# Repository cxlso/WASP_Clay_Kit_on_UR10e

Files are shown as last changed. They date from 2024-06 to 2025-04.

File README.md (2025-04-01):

# WASP Clay Kit on UR10e
###### A controller box and mounts to get started with the WASP Clay Kit on UR10e

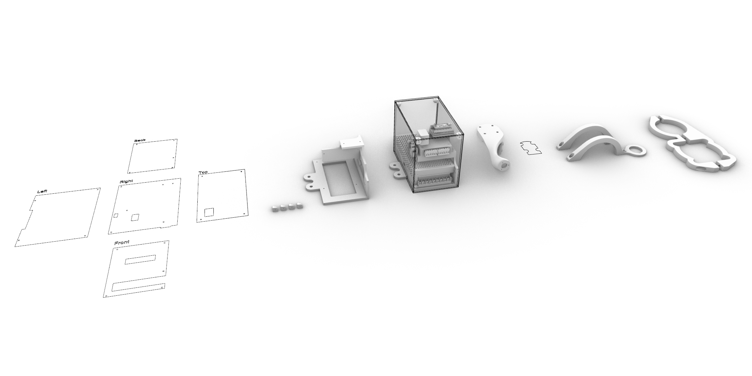
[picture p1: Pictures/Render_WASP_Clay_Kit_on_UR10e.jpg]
Render_MDPH2_on_UR10e


## Overview
This repository contains everything needed to get started with robotic clay printing with the [WASP Clay Kit](https://www.3dwasp.shop/en/prodotto/clay-extruder-wasp-clay-kit/) and the [Universal Robot UR10e](https://www.universal-robots.com/products/ur10-robot/) (or any UR model).

Included in the repository are:

- Controller Box CAD Files: For 3D printing the structure and laser cutting the acrylic walls of the controller box,
- Mounts CAD Files: For 3d printing mounts to secure the clay tank, extruder, and pressure gauge,
- Scripts: Arduino code for the controller and Grasshopper toolpath example.

## Note on the Signal Workflow

The workflow begins with the Grasshopper script embedding the extrusion commands (rate and direction) into the URP file. This file instructs the UR10e to output two analog voltage signals (0-5V) on AO0 (Pul) and AO1 (Dir). These signals are read by the Arduino on pins A0 (Pul) and A1 (Dir), which translates them into digital signals on pins D2 (Pul) and D3 (Dir) for the stepper motor driver, ultimately driving the WASP extruder's stepper motor.

The analog signals can also be overwritten in real-time using the UR Teaching Pendant.

**Grasshopper (Extrusion Command Embeded in URP file/G-Code ) ⟶ UR10e (Analog Output 0-5V) ⟶ Arduino (Analog Input) ⟶ Stepper Motor Driver (Digital Signal) ⟶ WASP Extruder's Stepper Motor**

## Components

- Arduino Nano
- TM6600 Stepper Motor Driver
- LM2596 Stepdown reducer 24v to 12v
- Rocker Switch
- 24v Power Supply
- M3 and M4 Hex Socket Head Screws
- 3mm Acrylic Sheet
- Electrical Connectors (JST XH in our case)
- 18 and 24awg cables 

## Setup and Installation
### Prerequisites

- UR10e Robotic Arm (or any UR models),
- WASP Clay kit (WASP LDM Extruder 3.0, Clay Tank),
- Rhino Grasshopper: For generating toolpath commands.

### Wiring Diagram

Refer to the following wiring diagram for the electrical connections.

LDM_WASP_Extruder_3.0_on_UR10e_Wiring_Diagram
Diagram made with the open-source tool [Fritzing](https://fritzing.org/).

### CAD Files

#### Controller Box

- [Structure](Controller_Box/CAD/Print_WASP_Skeleton.stl) 3D printing file. Skeleton inside de box holding all the components in place,
- [Corner brackets](Controller_Box/CAD/Print_WASP_Corner_Bracket.stl) 3D printing file,
- [3MM acrylic wall](Controller_Box/CAD/Cut_WASP_3MM_Walls.AI) Laser cutting file.

#### Mounts
- [WASP LDM Extruder 3.0 Mount](Mounts/Print_WASP_Extruder_Mount.stl) 3D printing file,
- [Clay Tank Mount](Mounts/Print_WASP_Tank_Mount.stl) 3D printing file,
- [Pressure Gauge Mount](Mounts/Print_WASP_Gauge_Mount.stl) 3D printing file.

If customization is desired, Rhino files for each of the parts are in the repository.

### Scripts

#### [Arduino Script](Arduino/Stepper_PulseDir_WASP)

Upload the provided code to the Arduino Nano. Ensure all connections are made according to the wiring diagram.

#### [Grasshopper Definition](Grasshopper/Basic_Robotic_Extrusion_WASP.gh)

The [Robots](https://www.food4rhino.com/en/app/robots) plugin is necessary. The extrusion rate is set in RPM and is converted to steps per second with the following equation:
$$y = \left( \frac{x \times 800}{60} \right)$$
Where 800 represents the number of steps per revolution for the stepper motor, and 60 is used to convert minutes to seconds, resulting in the conversion of RPM (x) to steps per second (y).

## Pictures and Videos

https://github.com/cxlso/WASP_Clay_Kit_on_UR10e/assets/29285706/da89046f-a3ae-4ad9-899d-0b77da0f6eef

      

## Contributing

Contributions are welcome! Please submit a pull request or open an issue to discuss any changes or improvements.

## License

[][cc-by-nc-sa]

This work is licensed under a
[Creative Commons Attribution-NonCommercial-ShareAlike 4.0 International License][cc-by-nc-sa].

[][cc-by-nc-sa]

[cc-by-nc-sa]: http://creativecommons.org/licenses/by-nc-sa/4.0/
[cc-by-nc-sa-image]: https://licensebuttons.net/l/by-nc-sa/4.0/88x31.png
[cc-by-nc-sa-shield]: https://img.shields.io/badge/License-CC%20BY--NC--SA%204.0-lightgrey.svg

## Acknowledgements

Special thanks to [Luigi Pacheco](https://luigipacheco.com/) and [Bhavleen Kaur](https://bhavleenkaurnarula.wordpress.com/) from the [FIU RDFlab](https://rdflabfiu.github.io/labwiki/) for the tips.

This project was developed on my own initiative at the [School of Architecture of Florida Atlantic University](https://www.fau.edu/artsandletters/architecture/) within the Environmental Design and Natural Materials lab, directed by Shermeen Yousif.

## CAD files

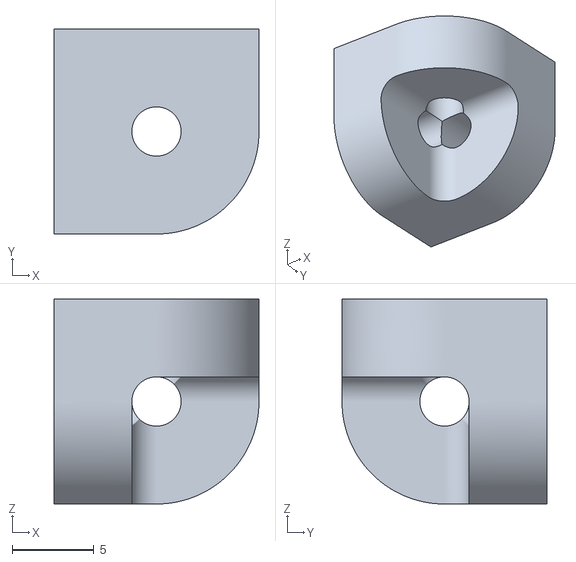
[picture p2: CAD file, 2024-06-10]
Controller_Box/CAD/Print_WASP_Corner_Bracket.stl
12.5 x 12.5 x 12.5

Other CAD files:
Controller_Box/CAD/Parts/Fan_40x40x20.3dm
Controller_Box/CAD/Parts/Nema_17HS24-2104S.3dm
Controller_Box/CAD/Parts/TB6600_Stepper_Motor_Driver.3dm
Mounts/UR10e_Flange.3dm

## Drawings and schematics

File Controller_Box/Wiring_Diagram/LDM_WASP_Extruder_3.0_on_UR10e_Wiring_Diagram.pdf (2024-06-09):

# UR10e Controller Box

# 110/220V AC

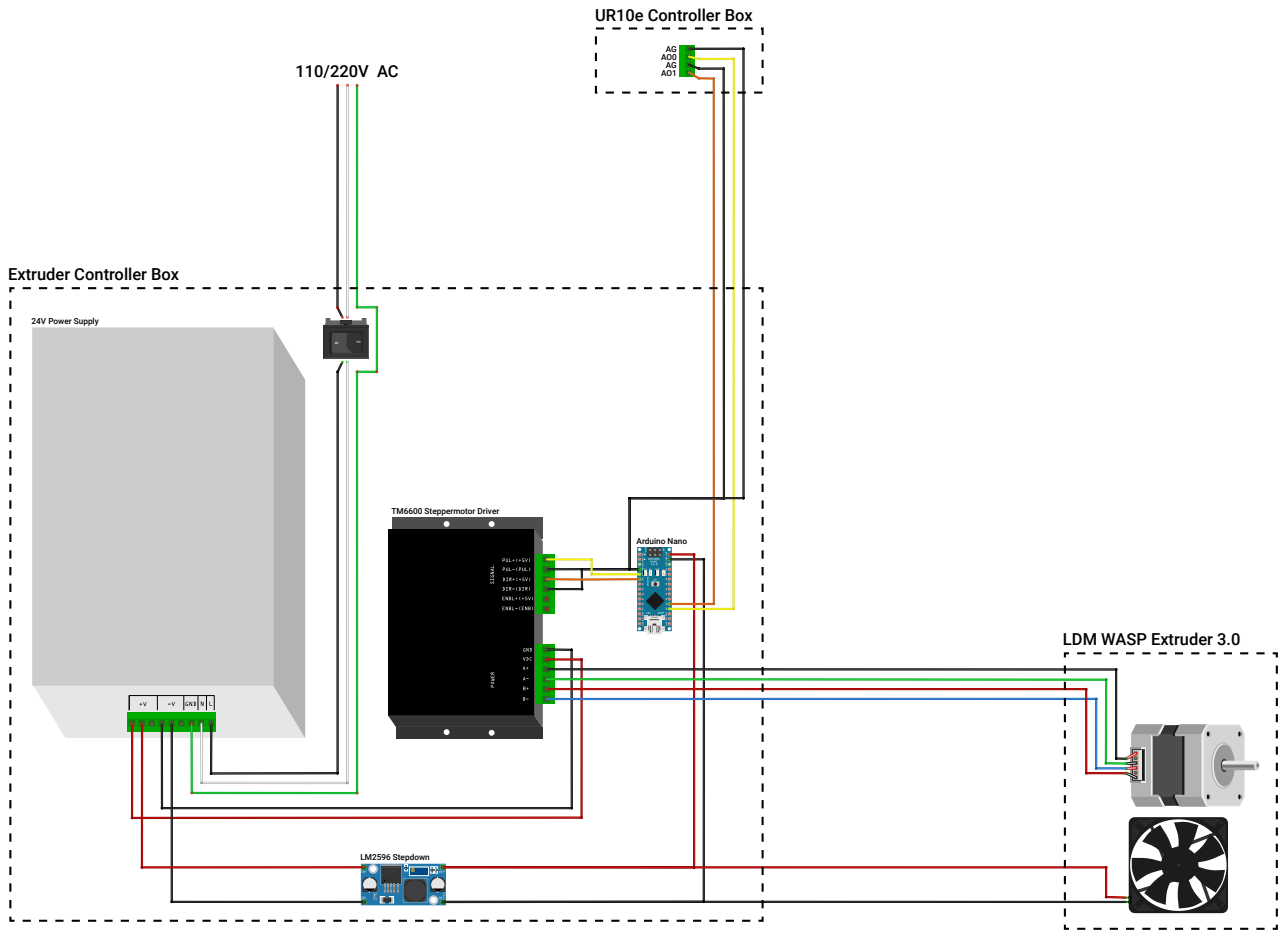
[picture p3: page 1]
LM2596 Stepdown; Arduino Nano; 24V Power Supply; TM6600 Steppermotor Driver

Extruder Controller Box

LDM WASP Extruder 3.0

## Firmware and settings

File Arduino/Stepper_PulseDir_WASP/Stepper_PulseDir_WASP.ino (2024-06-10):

/*
  Stepper Motor Extruder Pulse and Direction

  This Arduino sketch controls a stepper motor using analog signals for speed (Pul/Step) and direction (Dir).

  Author:   cxlso (cxl.so)
  Year:     2024
  Version:  1

  Hardware Compatibility:
  - Stepper motor-based extruders (e.g., LDM WASP Extruders, Massive Dimension MDPH2 Extruder)

  Library Dependencies:
  - AccelStepper library (https://www.airspayce.com/mikem/arduino/AccelStepper/)

  License: GNU General Public License, version 2 or later (GPL-2.0-or-later) (https://www.gnu.org/licenses/gpl-2.0.html)
*/



#include <AccelStepper.h>

// Define driver digital pin connections
#define PulPin 2
#define DirPin 3
#define EnaPin 4

// Create a new AccelStepper object
AccelStepper stepper(AccelStepper::DRIVER, PulPin, DirPin);



void setup() {

  // Define stepper maximum speed in steps per second (steps/s)
  stepper.setMaxSpeed(4000);

  // Enable stepper
  pinMode(EnaPin, OUTPUT);
  digitalWrite(EnaPin, HIGH);

}



void loop() {

  // Read sensor values
  int Step_Reading = analogRead(A0);
  int Dir_Reading = analogRead(A1);

  // Limit minimum speed
  if (Step_Reading < 100) Step_Reading = 0;

  // Map Step_Reading to a speed range from 0 to 4000 steps/s
  int stepperMotorSpeed = map(Step_Reading, 0, 1023, 0, 4000);
  // Map Dir_Reading to a voltage range from 0V to 5V
  float stepperMotorDir = map(Dir_Reading, 0, 1023, 0, 5);

  // Set motor direction and speed
  if (stepperMotorDir > 0.5) {
    stepper.setSpeed(-stepperMotorSpeed);
  } else {
    stepper.setSpeed(stepperMotorSpeed);
  }
  stepper.runSpeed();
  
}
